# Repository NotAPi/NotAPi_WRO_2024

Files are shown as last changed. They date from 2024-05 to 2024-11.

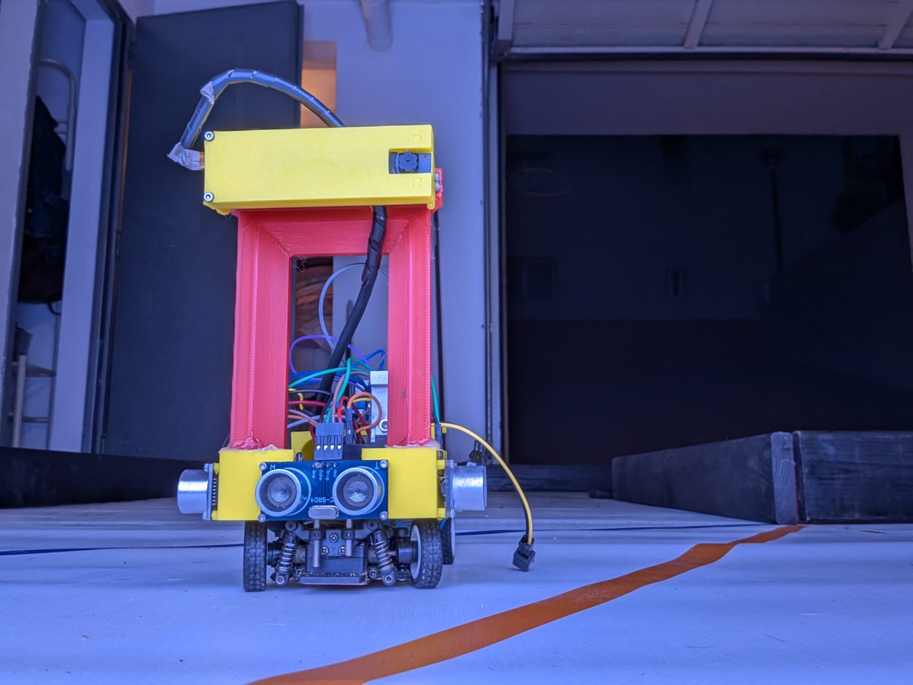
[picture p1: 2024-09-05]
Pictures/Vehicle/V2-NacionalVersion/WhatsApp Image 2024-09-05 at 20.47.06.jpeg

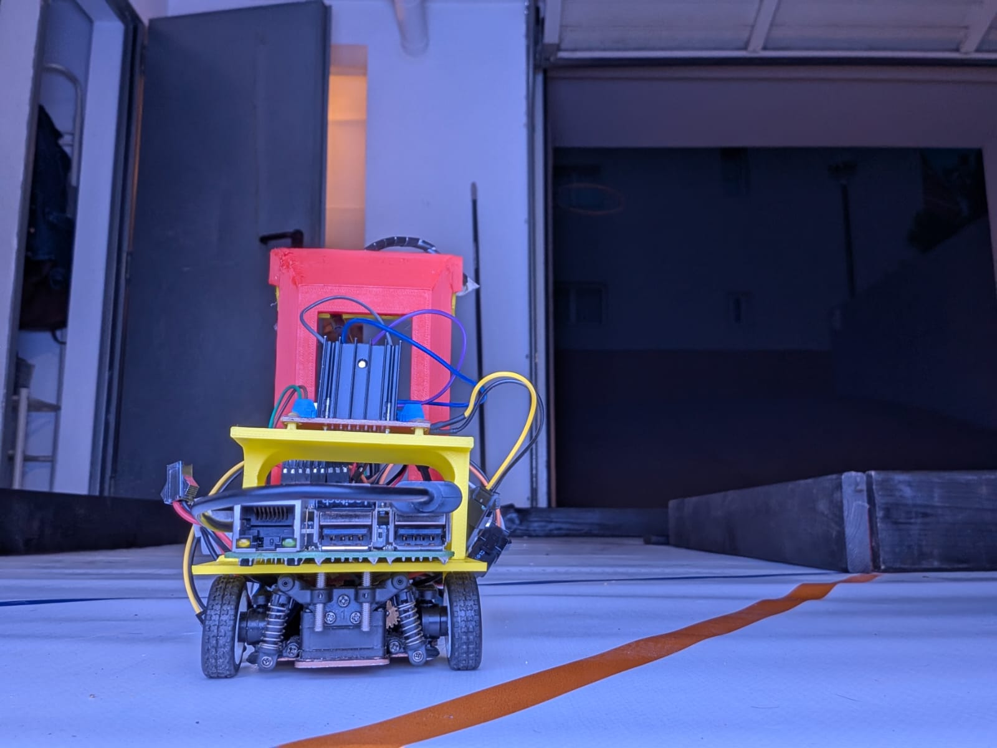
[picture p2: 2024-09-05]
Pictures/Vehicle/V2-NacionalVersion/WhatsApp Image 2024-09-05 at 20.47.07.jpeg

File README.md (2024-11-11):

# NotAPi_WRO_2024

## 1.Mobility Management
Our car is mounted on the baisis of a RC car of which we only kept the wheels and the central axle and the drive shaft of the front wheels. The direction is controlled by a servo connected to a crank that can turn 140º and the circular movment of the servo moves the crack horizontaly and that turns the wheels. A motor is mounted on this base connected to a gear that we designed and got printed on aluminium to make the car slower that gear is connected to the main axle, the motor is connected to a L298N unit. Every other structural part has been 3D printed.

------------------------------------------
## 2.Power and Sense Management
The battery is a lipo battery 4 Cells 850mAh 14.8V, connected to 2 different voltage regluators one feeding the motor at 16V and the other one feeds everything else at 5V mostly thru a pcb that we designed and had custom made.
The sensors are 3 lidars and 3 tofs connected to a raspberry pi 4 thru the pcb and screwed to the supporting structures mentioned previous section as of writing the camera is not yet mounted. Previously we used camera extracted from a laptop wich we might change for a raspberry picam 220º with fisheye lens.

-------------------------------------------------------------------
## 3.Obstacle Management
The car is designed to start measuring it's distance to the walls in front and the sides, by advancing until the front distance is about 20cm then stops checks to the sides decides the direction of rotation by checking wich side has a close wall and then turns to the correct side, repeats this process at every corner and after counting 12 times it should stop when the distance in front is within a margin of error of the distance at the beginning. We have yet to code the second part, the obstacle course

---------------------------------------------------------

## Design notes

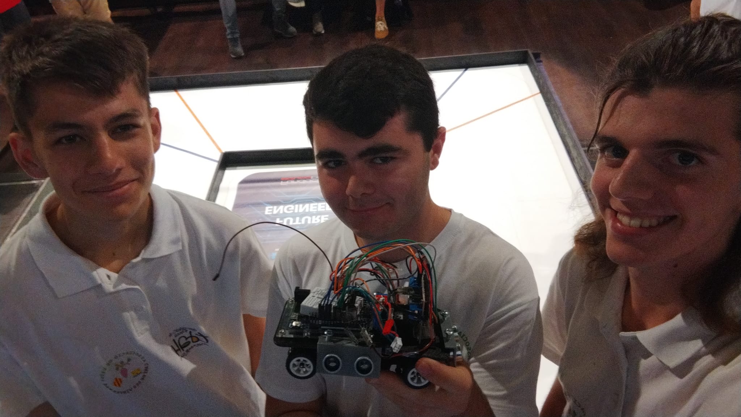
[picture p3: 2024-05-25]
Pictures/Team/Imagen de WhatsApp 2024-05-25 a las 09.47.15_d164381c.jpg

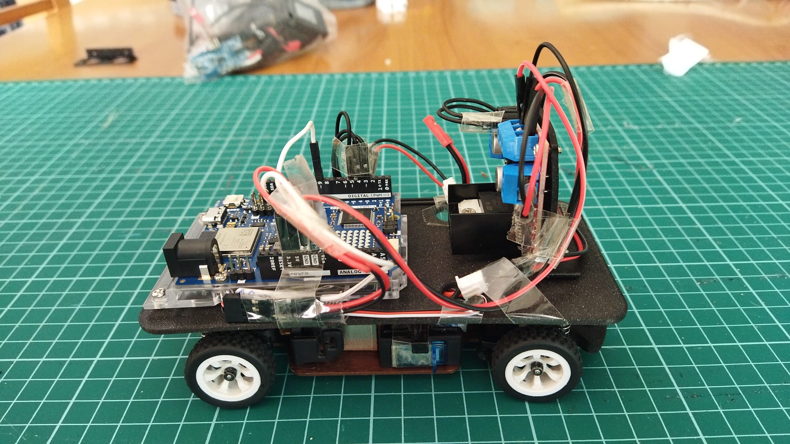
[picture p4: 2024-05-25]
Pictures/Vehicle/V1/Imagen de WhatsApp 2024-05-22 a las 17.22.16_14fc1476.jpg

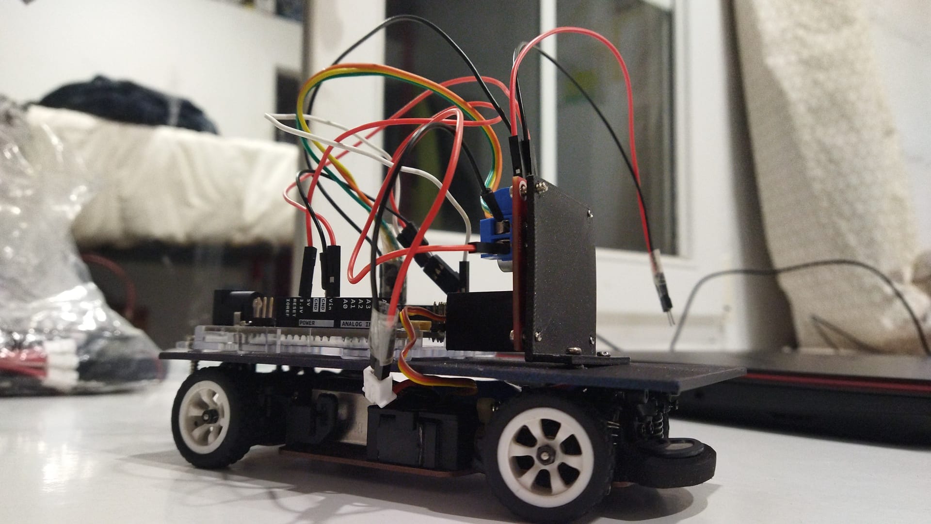
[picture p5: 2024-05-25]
Pictures/Vehicle/V1/Imagen de WhatsApp 2024-02-02 a las 21.30.41_242e0a9a.jpg

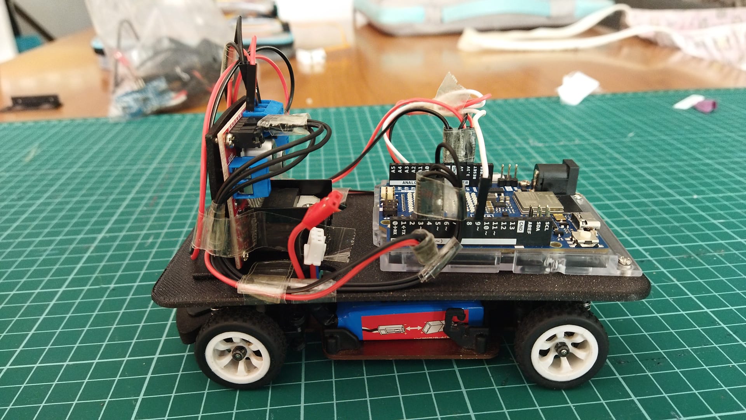
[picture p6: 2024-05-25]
Pictures/Vehicle/V1/Imagen de WhatsApp 2024-05-22 a las 17.22.16_61251b05.jpg

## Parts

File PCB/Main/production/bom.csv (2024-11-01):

Designator | Footprint | Quantity | Value | LCSC Part #
J1 | PinHeader_1x04_P2.54mm_Vertical | 1 | Lidar1
J10 | PinHeader_1x03_P2.54mm_Vertical | 1 | Conn_01x03
J2 | PinHeader_1x04_P2.54mm_Vertical | 1 | Lidar2
J3 | PinHeader_1x04_P2.54mm_Vertical | 1 | Lidar3
J4 | PinHeader_1x04_P2.54mm_Vertical | 1 | Lidar4
J5 | PinSocket_2x20_P2.54mm_Vertical | 1 | Raspberry_Pi_2_3
J6 | PinSocket_1x06_P2.54mm_Horizontal | 1 | ToF1
J7 | PinSocket_1x06_P2.54mm_Horizontal | 1 | ToF2
J8 | PinSocket_1x06_P2.54mm_Horizontal | 1 | ToF3
J9 | PinSocket_1x06_P2.54mm_Horizontal | 1 | ToF4
M1 | PinHeader_1x03_P2.54mm_Vertical | 1 | Motor_Servo
PLOGIC1, PMOTOR1 | PinHeader_1x04_P2.54mm_Vertical | 2 | ~
TP1, TP2 | TestPoint | 2 | TestPoint
U1 | TO-220-15_P2.54x2.54mm_StaggerOdd_Lead4.58mm_Vertical | 1 | L298N
U2 | CONN-TH_XT60 | 1 | XT60 | C98733

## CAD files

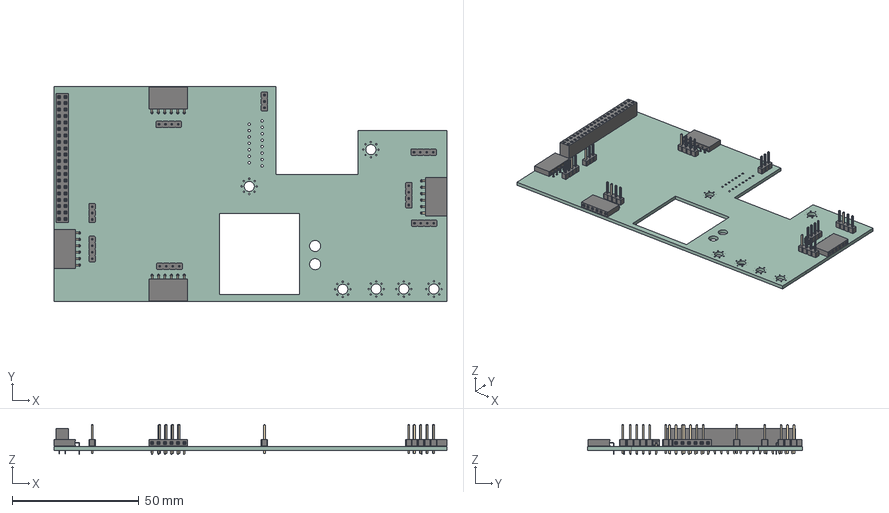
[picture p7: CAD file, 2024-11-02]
PCB/Main/Main.step
155.1 x 85.0 x 11.8 mm
PinSocket_2x20_P254mm_Vertical
PinHeader_1x04_P254mm_Vertical x 6
PinSocket_1x06_P254mm_Horizontal x 4
PinHeader_1x03_P254mm_Vertical x 2
Main_PCB

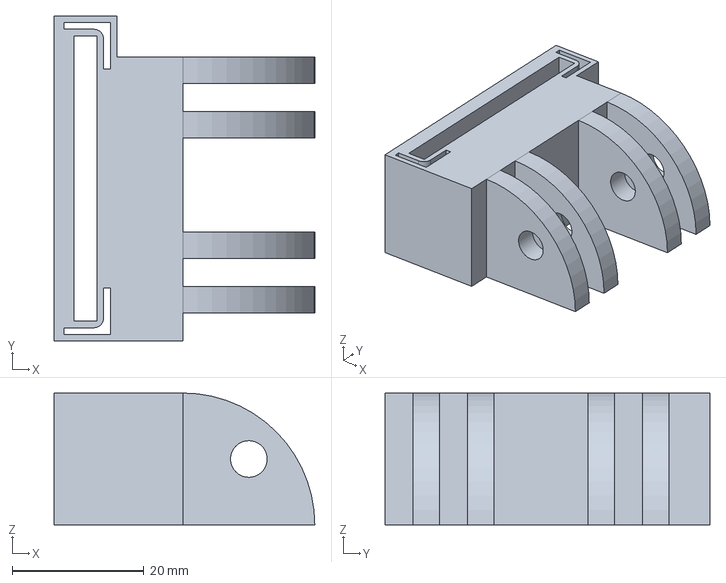
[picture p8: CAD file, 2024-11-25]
Models/CamSupport.FCStd
39.5 x 49.2 x 20.0 mm

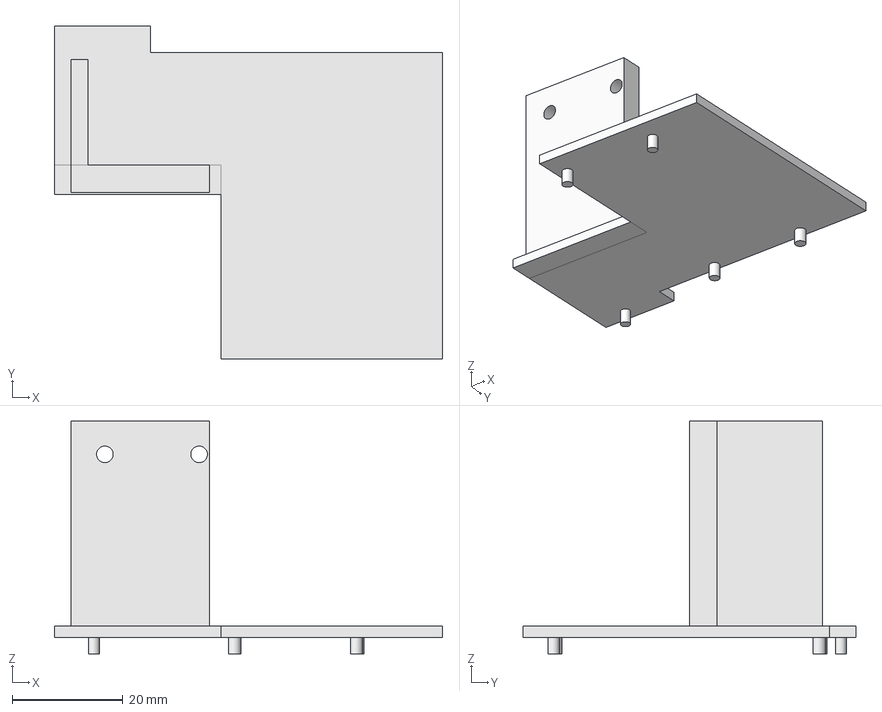
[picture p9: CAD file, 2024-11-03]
Models/JaraMODELOS3D/MOTORsoporteFINAL.FCStd
70.0 x 60.0 x 42.0 mm

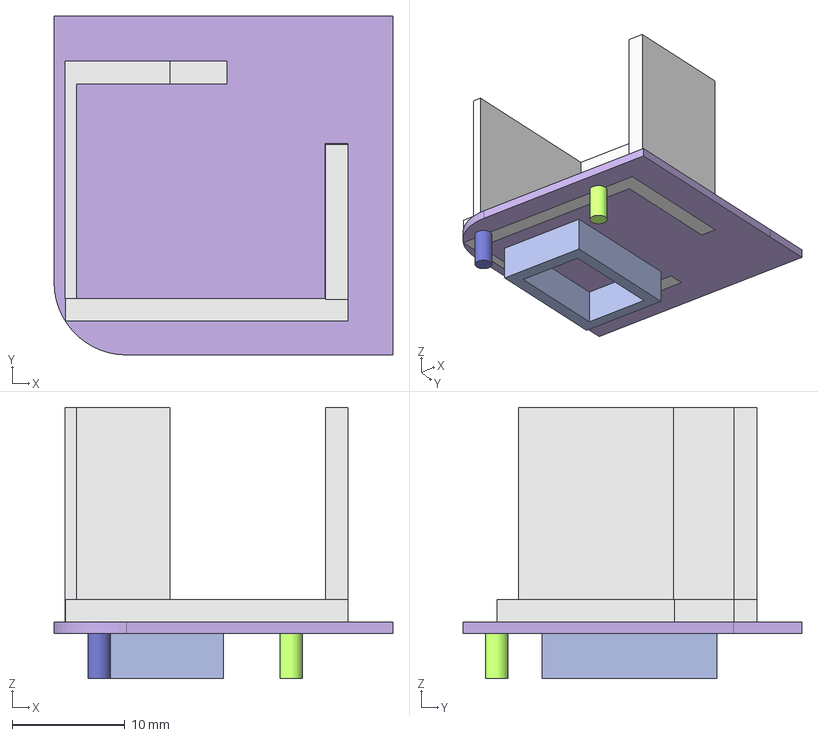
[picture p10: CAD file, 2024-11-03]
Models/JaraMODELOS3D/usados/SoporteMotor6.step
30.0 x 30.0 x 24.0 mm

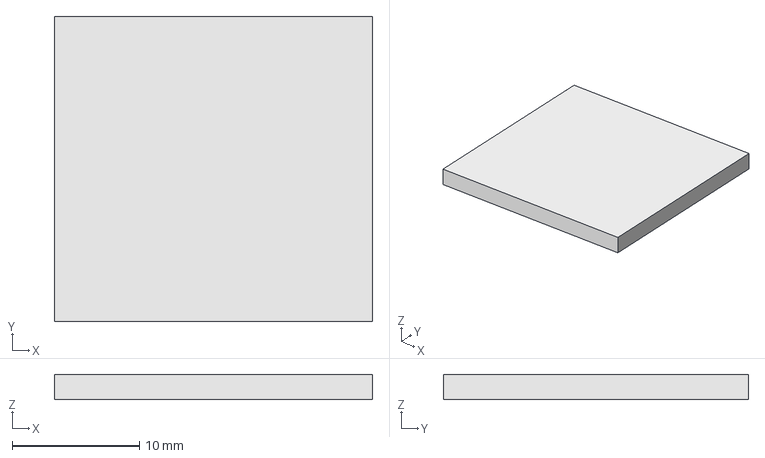
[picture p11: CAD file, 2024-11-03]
Models/JaraMODELOS3D/CAMARAsoporte.FCStd
25.0 x 24.0 x 2.00 mm

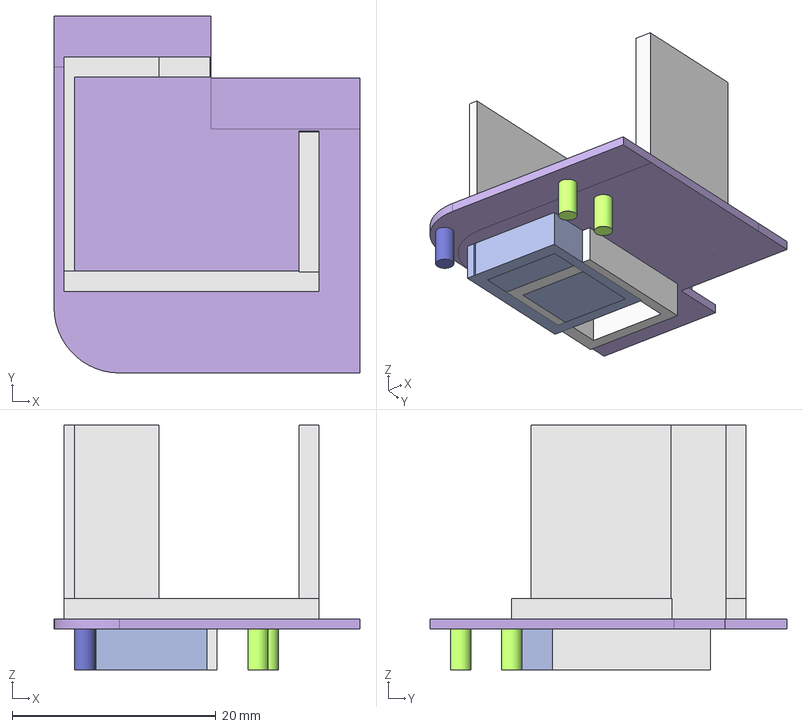
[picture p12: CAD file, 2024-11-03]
Models/JaraMODELOS3D/usados/SoporteMotorbueno3.step
30.0 x 35.0 x 24.0 mm
Sketch004
Sketch005
Sketch006
Sketch
Sketch001
Sketch002
Sketch003
Sketch007

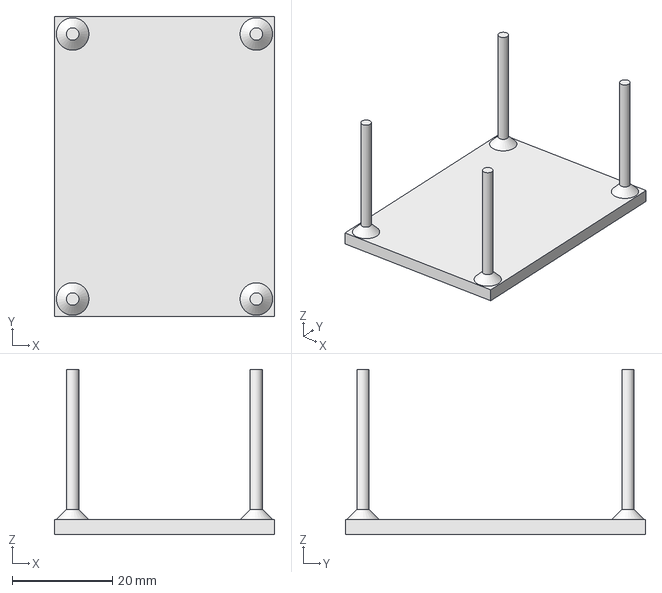
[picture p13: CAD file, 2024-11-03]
Models/JaraMODELOS3D/usados/ReguladorSoporte.step
44.0 x 60.0 x 33.0 mm

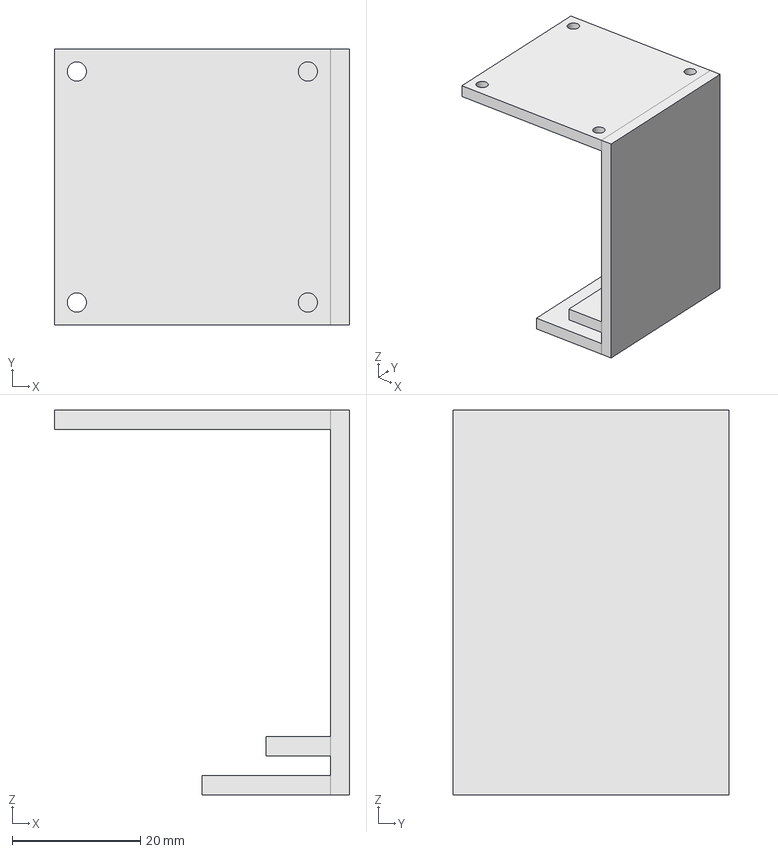
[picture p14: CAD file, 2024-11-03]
Models/L298Nsoporte.FCStd
46.0 x 43.0 x 60.0 mm

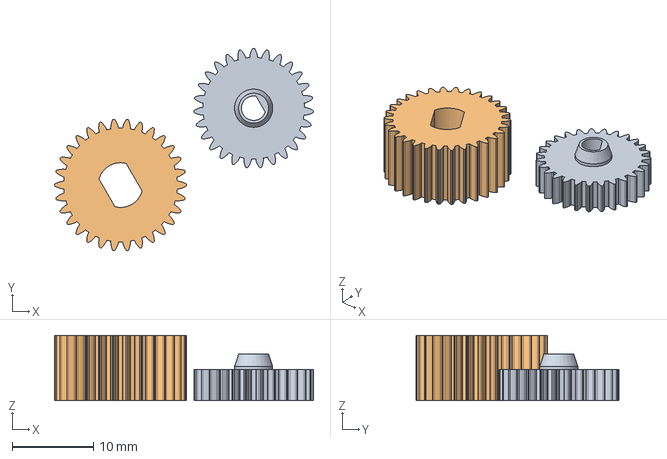
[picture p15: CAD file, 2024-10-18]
Models/GearAxis.FCStd
31.9 x 24.9 x 8.00 mm

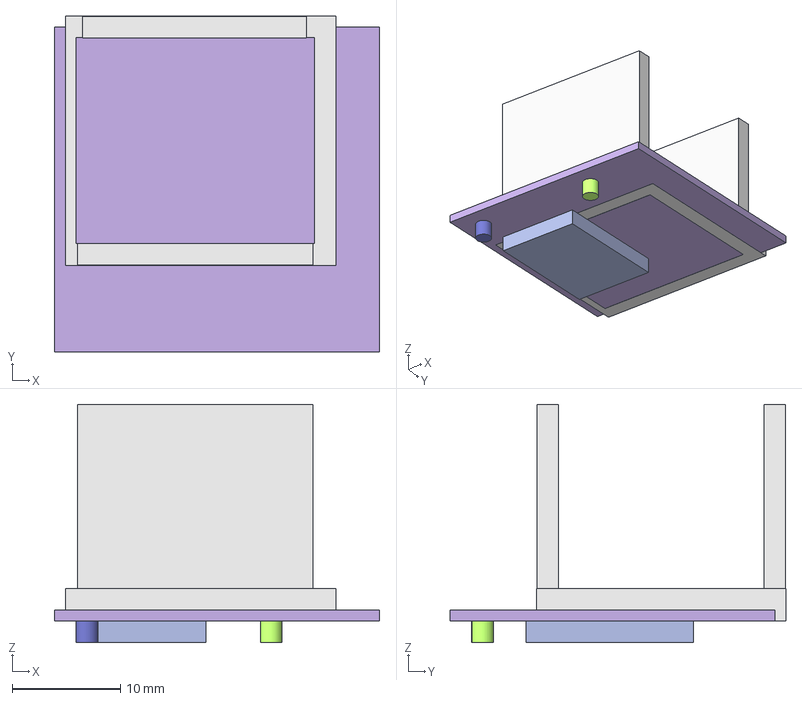
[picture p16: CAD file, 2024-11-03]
Models/JaraMODELOS3D/usados/SoporteMotor.step
30.0 x 31.0 x 22.0 mm
Sketch
Sketch001
Sketch002
Sketch003
Sketch004
Sketch005
Sketch006

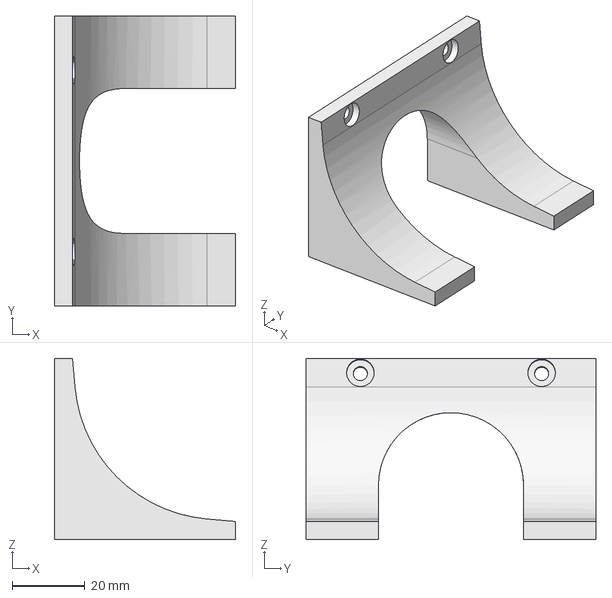
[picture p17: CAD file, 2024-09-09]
Models/woodSupport.FCStd
50.0 x 80.0 x 50.0 mm

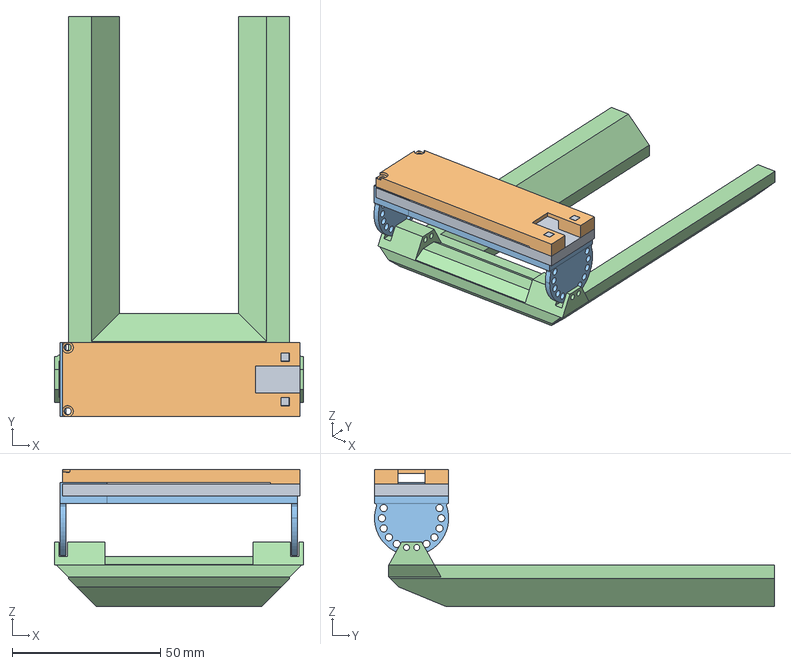
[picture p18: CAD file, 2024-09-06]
Models/camera.FCStd
84.0 x 134.8 x 46.3 mm

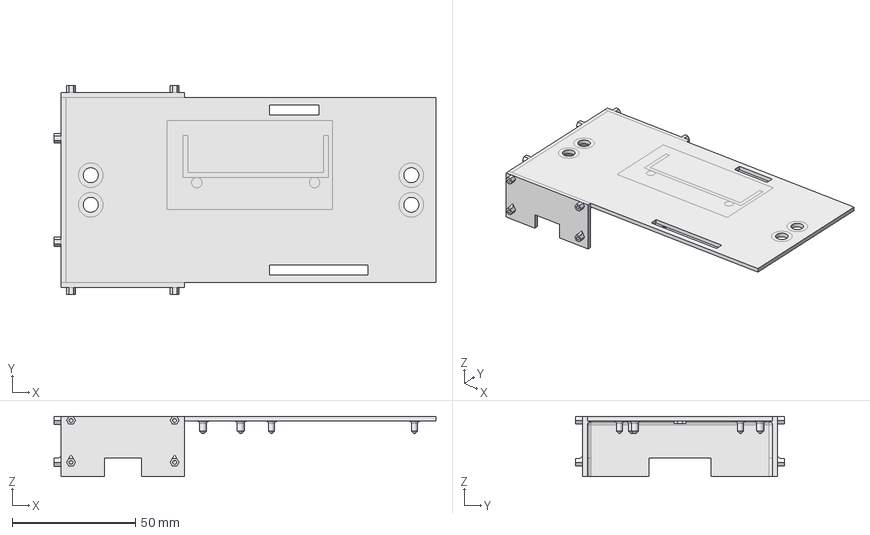
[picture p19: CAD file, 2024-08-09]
Models/car-Body001.step
154.9 x 84.8 x 24.5 mm

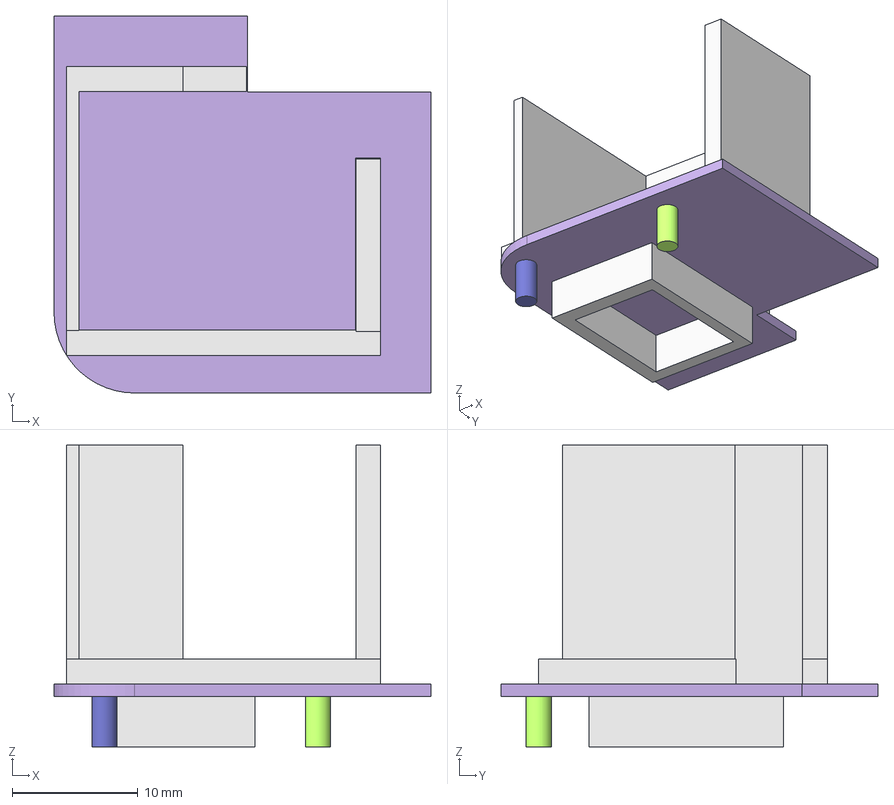
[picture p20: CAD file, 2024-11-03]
Models/JaraMODELOS3D/usados/SoporteMotorBueno4.step
30.0 x 30.0 x 24.0 mm

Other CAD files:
Models/MOTORsoporteFINAL3.step
Models/JaraMODELOS3D/Raspberry4soporte.FCStd
Models/JaraMODELOS3D/usados/newsuport.std.FCStd
Models/JaraMODELOS3D/usados/SoporteMotorMarcCOSA.FCStd
Models/JaraMODELOS3D/usados/L298Nsoporte1.step
Models/JaraMODELOS3D/usados/MOTORsoporteFINAL-Body.step
Models/JaraMODELOS3D/usados/MOTORsoporteFINAL.FCStd
Models/JaraMODELOS3D/usados/MOTORsoporteFINAL2.step
Models/JaraMODELOS3D/usados/ReguladorSoporte-Body.step
Models/JaraMODELOS3D/usados/ReguladorSoporte.FCStd
Models/JaraMODELOS3D/usados/ReguladorSoportenose.FCStd
Models/JaraMODELOS3D/usados/SoporteCam.FCStd
Models/JaraMODELOS3D/usados/SoporteMotor5.FCStd
Models/JaraMODELOS3D/usados/SoporteMotor5.step
Models/JaraMODELOS3D/usados/SoporteMotorBueno4.FCStd
Models/JaraMODELOS3D/usados/SoporteMotorbueno.step
Models/JaraMODELOS3D/usados/SoporteMotorbueno2.step
Models/car-Body001.stl
Models/car.FCStd
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

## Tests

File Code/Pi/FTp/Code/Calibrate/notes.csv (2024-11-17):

2m | 13.24 | 13.23 | 13.2
1m | 6.6
55º | 2.1 | 2.05 | 2.1
155º | 2.12 | 2.04 | 2.1

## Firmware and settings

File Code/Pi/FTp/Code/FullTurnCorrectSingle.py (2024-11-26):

import time
import pigpio
import os
import sys
import threading

try:
    os.system("sudo pigpiod")  # Launching GPIO library
    time.sleep(1)  # As it takes some time to launch
except:
    #aaaprint("GPIO library already launched")
    pass

# 55------105---155

# Initialize pigpio
pi = pigpio.pi()

L_RX_PIN = 22
R_RX_PIN = 24
F_RX_PIN = 25

IN1_PIN = 10
IN2_PIN = 11
ENA_PIN = 12

SERVO_PIN = 17

Ldistance = 0
Rdistance = 0
Fdistance = 0

lock = threading.Lock()


Laps = 0
# Try to close the serial connection if it is already open
try:
    pi.bb_serial_read_close(R_RX_PIN)
    pi.bb_serial_read_close(L_RX_PIN)
    pi.bb_serial_read_close(F_RX_PIN)
except:
    pass



# Set up the software serial connection
pi.set_mode(R_RX_PIN, pigpio.INPUT)
pi.bb_serial_read_open(R_RX_PIN, 115200)
pi.set_mode(L_RX_PIN, pigpio.INPUT)
pi.bb_serial_read_open(L_RX_PIN, 115200)
pi.set_mode(F_RX_PIN, pigpio.INPUT)
pi.bb_serial_read_open(F_RX_PIN, 115200)
#aaaprint("init done")

def parse_lidar_data(data):
    if len(data) >= 9 and data[0] == 0x59 and data[1] == 0x59:
        distance = data[2] + data[3] * 256
        strength = data[4] + data[5] * 256
        return distance, strength
    return None, None

def F_read_lidar():
    while True:
        (count, data) = pi.bb_serial_read(F_RX_PIN)
        if count > 0:
            break
    if count > 0:
        distance, strength = parse_lidar_data(data)
        if distance is not None: # Isn't really needed
            # #aaaprint(f"DistanceR: {distance} cm, Strength: {strength}")
            return distance

def R_read_lidar():
    while True:
        (count, data) = pi.bb_serial_read(R_RX_PIN)
        if count > 0:
            break
    if count > 0:
        distance, strength = parse_lidar_data(data)
        if distance is not None: # Isn't really needed
            # #aaaprint(f"DistanceR: {distance} cm, Strength: {strength}")
            return distance

def L_read_lidar():
    while True:
        (count, data) = pi.bb_serial_read(L_RX_PIN)
        if count > 0:
            break
    if count > 0:
        distance, strength = parse_lidar_data(data)
        if distance is not None: # Isn't really needed
            # #aaaprint(f"DistanceL: {distance} cm, Strength: {strength}")
            return distance
        
def forward(speed=255):
    pi.write(IN1_PIN, 0)
    pi.write(IN2_PIN, 1)
    pi.set_PWM_dutycycle(ENA_PIN, speed)

def backward(speed=255):
    pi.write(IN1_PIN, 1)
    pi.write(IN2_PIN, 0)
    pi.set_PWM_dutycycle(ENA_PIN, speed)

def stop():
    pi.write(IN1_PIN, 0)
    pi.write(IN2_PIN, 0)
    pi.set_PWM_dutycycle(ENA_PIN, 0)

def servo(angle=105):
    pulse_width = 500 + (angle / 180.0) * 2000
    pi.set_servo_pulsewidth(SERVO_PIN, pulse_width)

def turnRight(angle=90):
    stop()
    time.sleep(0.05)
    if angle == 90:
        servo(155)
        forward(255)
        time.sleep(1.95)

def turnLeft(angle=90):
    stop()
    time.sleep(0.05)
    if angle == 90:
        servo(55)
        forward(255)
        time.sleep(1.95)

def forwardm(distance=1):
    forward(255)
    time.sleep(6.6*distance)
    
def distance_loop():
    global Ldistance, Rdistance, Fdistance
    while True:
        Ldistance, Rdistance, Fdistance = L_Loop(), R_Loop(), F_Loop()
        print("L " + str(Ldistance) + " R " + str(Rdistance) + " F " + str(Fdistance))
        time.sleep(0.2)

def F_Loop():
    while True:
        FdistanceTemp1 = F_read_lidar()
        FdistanceTemp2 = F_read_lidar()

        # Fetry mechanism for invalid readings
        while (FdistanceTemp1 is None or 0 < FdistanceTemp1 > 500) or (FdistanceTemp2 is None or 0 < FdistanceTemp2 > 500):
            if FdistanceTemp1 is None or 0 < FdistanceTemp1 > 500:
                FdistanceTemp1 = F_read_lidar()
            if FdistanceTemp2 is None or 0 < FdistanceTemp2 > 500:
                FdistanceTemp2 = F_read_lidar()
            print(f"F Invalid readings: {FdistanceTemp1}, {FdistanceTemp2}")

        # Feturn the minimum of the two valid readings
        return min(FdistanceTemp1, FdistanceTemp2)

def L_Loop():
    while True:
        LdistanceTemp1 = L_read_lidar()
        LdistanceTemp2 = L_read_lidar()

        # Retry mechanism for invalid readings
        while (LdistanceTemp1 is None or 0 < LdistanceTemp1 > 500) or (LdistanceTemp2 is None or 0 < LdistanceTemp2 > 500):
            if LdistanceTemp1 is None or 0 < LdistanceTemp1 > 500:
                LdistanceTemp1 = L_read_lidar()
            if LdistanceTemp2 is None or 0 < LdistanceTemp2 > 500:
                LdistanceTemp2 = L_read_lidar()
            print(f"L Invalid readings: {LdistanceTemp1}, {LdistanceTemp2}")

        # Return the minimum of the two valid readings
        return min(LdistanceTemp1, LdistanceTemp2)

def R_Loop():
    while True:
        RdistanceTemp1 = R_read_lidar()
        RdistanceTemp2 = R_read_lidar()

        # Retry mechanism for invalid readings
        while (RdistanceTemp1 is None or 0 < RdistanceTemp1 > 500) or (RdistanceTemp2 is None or 0 < RdistanceTemp2 > 500):
            if RdistanceTemp1 is None or 0 < RdistanceTemp1 > 500:
                RdistanceTemp1 = R_read_lidar()
            if RdistanceTemp2 is None or 0 < RdistanceTemp2 > 500:
                RdistanceTemp2 = R_read_lidar()
            print(f"R Invalid readings: {RdistanceTemp1}, {RdistanceTemp2}")

        # Return the minimum of the two valid readings
        return min(RdistanceTemp1, RdistanceTemp2)
        
# def R_Loop():
#     global Rdistance
#     while True:
#         with lock:
#             RdistanceTemp = R_read_lidar()
#             if RdistanceTemp is not None and RdistanceTemp < 500:
#                 Rdistance = RdistanceTemp
#                 print(f"Rdistance updated: {Rdistance}")

#             time.sleep(0.1)

def distances():
    # Get Front distance    
    #aaaprint("F")
    FdistanceTemp = F_read_lidar()
    # #aaaprint("F:")
    if Fdistance is not None:
        Fdistance = FdistanceTemp               
    else:
        while True:
            Fdistance = F_read_lidar()
            if Fdistance is not None:
                break
    #aaaprint("F done")
    
    #aaaprint("L")
    
    # Get Left distance    
    Ldistance = L_read_lidar()
    # #aaaprint("L:")
    if Ldistance is None:
        try: 
            Ldistance = LdistanceOld
        except:
            while True:
                Ldistance = L_read_lidar()
                if Ldistance is not None:
                    break                
    else:
        LdistanceOld = Ldistance
    #aaaprint("L done")
    
    #aaaprint("R")
    # Get Right distance    
    Rdistance = R_read_lidar()
    # #aaaprint("R:")
    if Rdistance is None:
        try: 
            Rdistance = RdistanceOld
        except:
            while True:
                Rdistance = R_read_lidar()
                if Rdistance is not None:
                    break                
    else:
        RdistanceOld = Rdistance
    #aaaprint("R done")
    #aaaprint("return")
    return Ldistance, Rdistance, Fdistance

def distance_loop():
    global Ldistance, Rdistance, Fdistance
    while True:
        with lock:
            Ldistance, Rdistance, Fdistance = L_Loop(), R_Loop(), F_Loop()
            print("L " + str(Ldistance) + " R " + str(Rdistance) + " F " + str(Fdistance))
            time.sleep(0.2)

def turnLeftFull():
    servo(105)
    forwardm(0.2)
    turnLeft(90)
    
    servo()
    # forwardm(0.5)

    stop()
    time.sleep(0.05)
    #aaaprint("read")
    forward()
    time.sleep(0.1)
    Ldistance, Rdistance, Fdistance = L_Loop(), R_Loop(), F_Loop()
    #aaaprint("read done")
    stop()
    #aaaprint("L " + str(Ldistance) + " R " + str(Rdistance) + " SUM " + str(Ldistance + Rdistance) + " F " + str(Fdistance))

    while Ldistance + Rdistance > 150:
        forward()
        Ldistance, Rdistance, Fdistance = L_Loop(), R_Loop(), F_Loop()
        #aaaprint("L " + str(Ldistance) + " R " + str(Rdistance) + " SUM " + str(Ldistance + Rdistance) + " F " + str(Fdistance))
        # forward()        
        time.sleep(0.2)
    #aaaprint("Stop")
    time.sleep(0.05)    
    stop()
    
def turnRightFull():
    servo(105)
    forwardm(0.2)
    turnRight(90)
    
    servo()
    # forwardm(0.5)

    stop()
    time.sleep(0.05)
    #aaaprint("read")
    forward()
    time.sleep(0.1)
    Ldistance, Rdistance, Fdistance = L_Loop(), R_Loop(), F_Loop()
    #aaaprint("read done")
    stop()
    #aaaprint("L " + str(Ldistance) + " R " + str(Rdistance) + " SUM " + str(Ldistance + Rdistance) + " F " + str(Fdistance))

    while Ldistance + Rdistance > 150:
        forward()
        Ldistance, Rdistance, Fdistance = L_Loop(), R_Loop(), F_Loop()
        #aaaprint("L " + str(Ldistance) + " R " + str(Rdistance) + " SUM " + str(Ldistance + Rdistance) + " F " + str(Fdistance))
        # forward()        
        time.sleep(0.2)
    #aaaprint("Stop")
    time.sleep(0.05)    
    stop()

def main():
    global Ldistance, Rdistance, Fdistance
    try:
        servo()
        time.sleep(0.05)
        forward()
        giros = 0
        while True:
            Ldistance, Rdistance, Fdistance = L_Loop(), R_Loop(), F_Loop()
            while Ldistance < 100 or Rdistance < 100:
                forward()
                Ldistance, Rdistance= L_Loop(), R_Loop()
                print("L " + str(Ldistance) + " R " + str(Rdistance) + " SUM " + str(Ldistance + Rdistance) + " F " + str("noneneneenene"))
                time.sleep(0.2)
                if Ldistance + Rdistance > 110:
                    break
            #aaaprint("Turn time")
            
            if Ldistance > Rdistance:
                turnLeftFull()
                giros = giros + 1
                #aaaprint("Left")
            
            if Rdistance > Ldistance:
                turnRightFull()
                giros = giros + 1
                #aaaprint("Right")
            forward()
            Ldistance, Rdistance, Fdistance = L_Loop(), R_Loop(), F_Loop()


            while int(Fdistance) > 165:
                forward()
                Ldistance, Rdistance, Fdistance = L_Loop(), R_Loop(), F_Loop()
                print("L " + str(Ldistance) + " R " + str(Rdistance) + " SUM " + str(Ldistance + Rdistance) + " F " + str(Fdistance))
                time.sleep(0.2)
                #aaaprint ("F " + str(Fdistance))
                if int(Fdistance) < 165:
                    break
            
            if giros == 12:
                break
            #aaaprint("150")
            
            #aaaprint("Correct time")
            Ldistance, Rdistance, Fdistance = L_Loop(), R_Loop(), F_Loop()
            #aaaprint("L " + str(Ldistance) + " R " + str(Rdistance) + " SUM " + str(Ldistance + Rdistance) + " F " + str(Fdistance))
            stop()
            
            if Ldistance > Rdistance * 0.9:
                servo(95)  # Turn left
                #aaaprint("90")
            elif Rdistance > Ldistance * 0.9:
                servo(115)  # Turn right
                #aaaprint("120")
            else:
                servo(105)  # Go straight
                #aaaprint("105")
            forwardm(0.1)
            servo()
        
            for a in range(5):
                print(giros)
            
        stop()            

    except KeyboardInterrupt:
        stop()
        pi.bb_serial_read_close(R_RX_PIN)  # Close the serial connection on exit
        pi.bb_serial_read_close(L_RX_PIN)  # Close the serial connection on exit
        pi.bb_serial_read_close(F_RX_PIN)  # Close the serial connection on exit

        pi.stop()
        
if __name__ == "__main__":
    try:
        main()
    except KeyboardInterrupt:
        stop()
        pi.bb_serial_read_close(R_RX_PIN)  # Close the serial connection on exit
        pi.bb_serial_read_close(L_RX_PIN)  # Close the serial connection on exit
        pi.bb_serial_read_close(F_RX_PIN)  # Close the serial connection on exit

        pi.stop()    
    
    

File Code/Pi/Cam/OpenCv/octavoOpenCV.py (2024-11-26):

import cv2
import numpy as np
from picamera2 import Picamera2
import time
import pigpio
import os

try:
    os.system("sudo pigpiod")  # Launching GPIO library
    time.sleep(1)  # As it takes some time to launch
except:
    #aaaprint("GPIO library already launched")
    pass

# Initialize the Raspberry Pi camera
picam2 = Picamera2()
picam2.configure(picam2.create_preview_configuration(main={"size": (640, 480)}))
picam2.start()

IN1_PIN = 10 #motor pins
IN2_PIN = 11
ENA_PIN = 12

SERVO_PIN = 17 #servo pin
angulo_objetivo = 105 #lo pone en el centro 

# Initialize pigpio
pi = pigpio.pi()

# Allow the camera to warm up
time.sleep(0.1)

def forward(speed=255):
    pi.write(IN1_PIN, 0)
    pi.write(IN2_PIN, 1)
    pi.set_PWM_dutycycle(ENA_PIN, speed)

def servo(angle):
    pulse_width = 500 + (angle / 180.0) * 2000
    pi.set_servo_pulsewidth(SERVO_PIN, pulse_width)

primera_vuelta = True

while True:
    image_bgr = picam2.capture_array()

    # Swap the red and blue channels
    image = cv2.cvtColor(image_bgr, cv2.COLOR_BGR2RGB)

    cv2.waitKey(1)


    altura, anchura = image.shape[:2]  # Obtener las dimensiones de la imagen
    p1_izquierda = (anchura // 2, 0) 
    p2_izquierda = (0, altura)
    p1_derecha = ( anchura // 2, 0) 
    p2_derecha = (anchura, altura) 

    hsv_image = cv2.cvtColor(image, cv2.COLOR_RGB2HSV)
    lower_red1 = np.array([120, 100, 100])
    upper_red1 = np.array([150, 255, 255])
    lower_green = np.array([35, 100, 50])
    upper_green = np.array([85, 255, 255])

    red_mask = cv2.inRange(hsv_image, lower_red1, upper_red1)
    green_mask = cv2.inRange(hsv_image, lower_green, upper_green)

    def draw_centroids_and_contours(mask, image, color, mask2, color2):
        contours, _ = cv2.findContours(mask, cv2.RETR_EXTERNAL, cv2.CHAIN_APPROX_SIMPLE)
        contours2, _ = cv2.findContours(mask2, cv2.RETR_EXTERNAL, cv2.CHAIN_APPROX_SIMPLE)

        bloque_cercano = -1
        bloque_centro_x = -1  # Coordenada X del bloque más bajo
        bloque_color = None  # Color del bloque más bajo (para dibujar)
        verde = (0, 255, 0)
        rojo = (0, 0, 255)

        for contour in contours:
            M = cv2.moments(contour)
            if M["m00"] > 200:  # Ajusta este umbral para ignorar ruido area de los bloques
                cX = int(M["m10"] / M["m00"])
                cY = int(M["m01"] / M["m00"])
                cv2.drawContours(image, [contour], -1, color, 2)
                cv2.circle(image, (cX, cY), 3, color, -1)
                cv2.putText(image, "center", (cX - 20, cY - 20), cv2.FONT_HERSHEY_SIMPLEX, 0.5, color, 2)
                cv2.line(image, (0, cY), (image.shape[1], cY), color, 1)
                cv2.line(image, (cX, 0), (cX, image.shape[0]), color, 1)


                if cY > bloque_cercano:
                    bloque_cercano = cY
                    bloque_centro_x = cX
                    bloque_color = rojo
        
        for contour in contours2:
            M = cv2.moments(contour)
            if M["m00"] > 200:  # Ajusta este umbral para ignorar ruido area de los bloques
                cX = int(M["m10"] / M["m00"])
                cY = int(M["m01"] / M["m00"])
                cv2.drawContours(image, [contour], -1, color2, 2)
                cv2.circle(image, (cX, cY), 3, color2, -1)
                cv2.putText(image, "center", (cX - 20, cY - 20), cv2.FONT_HERSHEY_SIMPLEX, 0.5, color2, 2)
                cv2.line(image, (0, cY), (image.shape[1], cY), color2, 1)
                cv2.line(image, (cX, 0), (cX, image.shape[0]), color2, 1)


                if cY > bloque_cercano:
                    bloque_cercano = cY
                    bloque_centro_x = cX
                    bloque_color = verde

        if bloque_cercano != -1:
            cv2.line(image, (bloque_centro_x, 0), (bloque_centro_x, image.shape[0]), (255, 0, 255), 2) 

            if bloque_color == rojo:
                # Intersección con la línea izquierda
                x_interseccion_izq = p1_izquierda[0] + ((bloque_cercano - p1_izquierda[1]) / (p2_izquierda[1] - p1_izquierda[1])) * (p2_izquierda[0] - p1_izquierda[0]) #calculla 
                objetivo = int(x_interseccion_izq)
                diferencia_izq = bloque_centro_x - x_interseccion_izq

                diferencia_izq_normalizada = 105 + (diferencia_izq / anchura) * (155 - 55)
                diferencia_izq_normalizada = max(55, min(155, diferencia_izq_normalizada))
                cv2.putText(image, f"diferencia_izq: {diferencia_izq_normalizada}", (20, 60), cv2.FONT_HERSHEY_SIMPLEX, 0.5, (255, 0, 0), 2)
                servo(diferencia_izq_normalizada)

            else:
                # Intersección con la línea derecha
                x_interseccion_der = p1_derecha[0] + ((bloque_cercano - p1_derecha[1]) / (p2_derecha[1] - p1_derecha[1])) * (p2_derecha[0] - p1_derecha[0])
                objetivo = int(x_interseccion_der)
                diferencia_der = bloque_centro_x - x_interseccion_der

                diferencia_der_normalizada = 105 + (diferencia_der / anchura) * (155 - 55)
                diferencia_der_normalizada = max(55, min(155, diferencia_der_normalizada))
                cv2.putText(image, f"diferencia_izq: {diferencia_der_normalizada}", (20, 60), cv2.FONT_HERSHEY_SIMPLEX, 0.5, (255, 0, 0), 2)
                servo(diferencia_der_normalizada)

            

            cv2.arrowedLine(image, (bloque_centro_x, bloque_cercano), (objetivo, bloque_cercano), bloque_color, thickness=5, line_type=cv2.LINE_8, shift=0, tipLength=0.1)
            arrow_length = abs(bloque_centro_x - objetivo)
            cv2.putText(image, f"Arrow length: {arrow_length}", (20, 20), cv2.FONT_HERSHEY_SIMPLEX, 0.5, (255, 0, 0), 2)
            angulo_objetivo = 55 + (arrow_length / anchura) * (155 - 55)
            cv2.putText(image, f"servo: {angulo_objetivo}", (20, 40), cv2.FONT_HERSHEY_SIMPLEX, 0.5, (255, 0, 0), 2)
            #servo(angulo_objetivo)
        else:
            servo(105)





    draw_centroids_and_contours(red_mask, image, (0, 0, 255), green_mask, (0, 255, 0))
    
    
    cv2.line(image, p1_izquierda, p2_izquierda, (0, 255, 255), 2)
    cv2.line(image, p1_derecha, p2_derecha, (0, 255, 255), 2)

    cv2.imshow('Red Mask', red_mask)
    cv2.imshow('Green Mask', green_mask)
    cv2.imshow('original', image)

    if primera_vuelta == True:
        time.sleep(5)
        primera_vuelta = False
    
    forward() #Ve hacia adelante


    if cv2.waitKey(1) & 0xFF == ord('q'):
        pi.write(IN1_PIN, 0)
        pi.write(IN2_PIN, 0)
        pi.set_PWM_dutycycle(ENA_PIN, 0)
        break

cv2.destroyAllWindows()

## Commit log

2024-02-23 Servo y motor, pero no funciona el motor
2024-05-24 update
    update
    [car.FCStd, ultrasonic-Body.stl, ultrasonic-Body001.stl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]
2024-05-24 error de exceso de medida
    [PrimerSeguidor.ino]
2024-05-25 codigo que +- funciona 2
2024-07-19 UPDATE
    a
    [car.FCStd]
2024-07-26 udpdate models
    [car-Body001.step, car-Body001.stl, car.FCStd]
2024-08-19 Codigo kalma, funciona la medicion pero no la prueba insitu
2024-08-31 voy a intentar que funcione pero super fácil y casi sin usar los sensores pq la cosa no va tío :((((
2024-09-05 Rename Pictures/Vehicle/Imagen de WhatsApp 2024-02-02 a las 21.30.41_242e0a9a.jpg to Pictures/Vehicle/V1/Imagen de WhatsApp 2024-02-02 a las 21.30.41_242e0a9a.jpg
2024-11-08 moved obsolete files
    [GearAxis.FCStd, camera.FCStd, car-Body001.step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]
2024-11-08 more obsolete files
    [CAMARAsoporte.FCStd, L298Nsoporte.FCStd, L298Nsoporte1.step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]
2024-11-14 Contorno, centroide, mascaras, y ejes de rojo y verde
2024-11-15 Video seguidor de 1 bolque verde y 1 rojo
2024-11-16 varios centroides, varios objeos de la camara contorno
2024-11-17 detecta el bloque más cercano
2024-11-17 working code no camera
    [notes.csv]
2024-11-24 puñetalteclao
    [4to1Servosiganlforplanes-B_Cu.gbr, 4to1Servosiganlforplanes-B_Mask.gbr, 4to1Servosiganlforplanes-B_Paste.gbr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]
